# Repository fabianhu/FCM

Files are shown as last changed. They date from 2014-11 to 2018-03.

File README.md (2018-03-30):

FCM
===

FCM Flight Controller Firmware

Contents:

	Bootloader - the bootloader AVR32 project
	
	doc -  the main documentation folder -> read FCM Manual.pdf.
	
	hardware - here are the hardware sources. "hexa2wide" is our board. The actual physically produced board is under versions. This is the next release!
	
	software - the FCM copter control firmware main project

Size & weight:

	45 x 27 x 8 mm
	10 g

CPU:

	AVR32 UC3B0256
	32 bit
	48MHz

Sensors:

	Gyroscope (3 axis)
	Accelometer (3 axis)
	Magnetometer (3 axis)
	Barometer

Interfaces:

	4x PPM input or
	Receiver serial input for SPEKTRUM and HoTT or
	Receiver PPM sum signal input
	2x extra TTL USART (for Bluetooth, GPS, Telemetry etc.)
	6x PPM output for speed controllers (SimonK firmware recommended)
	optocoupler for 5 PPM outputs (placement variant)
	Pulse input for ultrasonic distance measurement
	USB for configuration and updates

Software features:

	FabOS32 RTOS
	Quaternion based attitude control
	Altitude hold
	Any copter configuration via mixing matrix
	RC compatibility
	HoTT SUMD receiver signal
	SPEKTRUM sattelite receiver signal
	4-channel "any RX" classic mode
	PPM sum signal
	USB Bootloader
	GPS integration with waypoint processing and return-to-home
	Throw to start
	
Telemetry

	HoTT telemetry with settings menue
	Bluetooth telemetry with settings menue, Attitude and graph display
	MAVlink prepared
	PID setting via extra RC analog channels

Software is "closed source" = all own code with minor extensions with LGPL
	Software is now open-sourced under GPL V3

Visit also the projects:
	FCM-android and
	FCM-Manager

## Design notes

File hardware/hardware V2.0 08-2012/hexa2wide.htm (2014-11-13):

Stückliste exportiert aus C:/Users/Fabi/Desktop/quadcopter_svn/versions/hardware V2.0 08-2012/hexa2wide.sch am 13.09.2012 19:53:36

Menge | Wert | Device | Bauteile
1 | | R-EU_R0603 | RL
7 | 2.2uF | C-EUC0603K | C4, C12, C13, C15, CA4, CP3, CR3
7 | 2k2 | R-EU_R0402 | R3, R6, R7, R8, R9, RS1, RS2
2 | 4µ7 | C-EUC0805 | CA2, CU1
3 | 4WIRE_CONN | 4WIRE_CONN | U$10, U$11, U$12
1 | 8MHz | CRYSTALCTS406 | Q1
1 | 10n 25V | C-EUC0402 | CR2
2 | 18pF | C-EUC0402 | CQ1, CQ2
2 | 39 | R-EU_R0402 | R1, R2
13 | 100n | C-EUC0402 | C1, C5, C6, C7, C14, CA1, CP1, CP2, CP4, CP5, CP6, CPR, CR1
1 | 220n | C-EUC0402 | CA3
8 | 330 | R-EU_R0402 | R11, R13, R15, R17, R19, RL1, RL2, RL3
1 | AT32UC3B0 | AT32UC3B0 | U$1
1 | BMP085 | BMP085 | U$9
1 | L3G4200DHAND | L3G4200DHAND | U$5
1 | LSM303HAND | LSM303HAND | U$7
1 | MCP1824ST-3302E/DB | MCP1824ST-3302E/DB | U1
1 | QS6J1=FDC6312P | QS6J1=FDC6312P | T1
1 | TLP283 | TLP283 | OK3
1 | TLP283-4 | TLP283-4 | OK1
5 | TPB1,27 | TPB1,27 | RST, TCK, TDI, TDO, TMS
6 | TPSQTP10SQ | TPSQTP10SQ | TP19, TP20, TP21, TP22, TP23, TP24
18 | TPSQTP16SQ | TPSQTP16SQ | TP1, TP2, TP3, TP4, TP5, TP6, TP7, TP8, TP9, TP10, TP11, TP12, TP13, TP14, TP15, TP16, TP17, TP18
1 | UBB_MICRO_HIROSE | UBB_MICRO_HIROSE | U$4
1 | blue | LEDCHIP-LED0603 | LED3
1 | green | LEDCHIP-LED0603 | LED2
1 | red | LEDCHIP-LED0603 | LED1

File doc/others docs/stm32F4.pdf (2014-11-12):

## stm32F4 Project

# 1. Description

## 1.1. Project

Project Name | stm32F4
Generated with: | STM32CubeMX 4.1.0
Date | 04/21/2014

## 1.2. MCU

MCU Serie | STM32F4
MCU Line | STM32F401
MCU name | STM32F401RETx
MCU Package | LQFP64
MCU Pin number | 64

# 2. Pinout Configuration

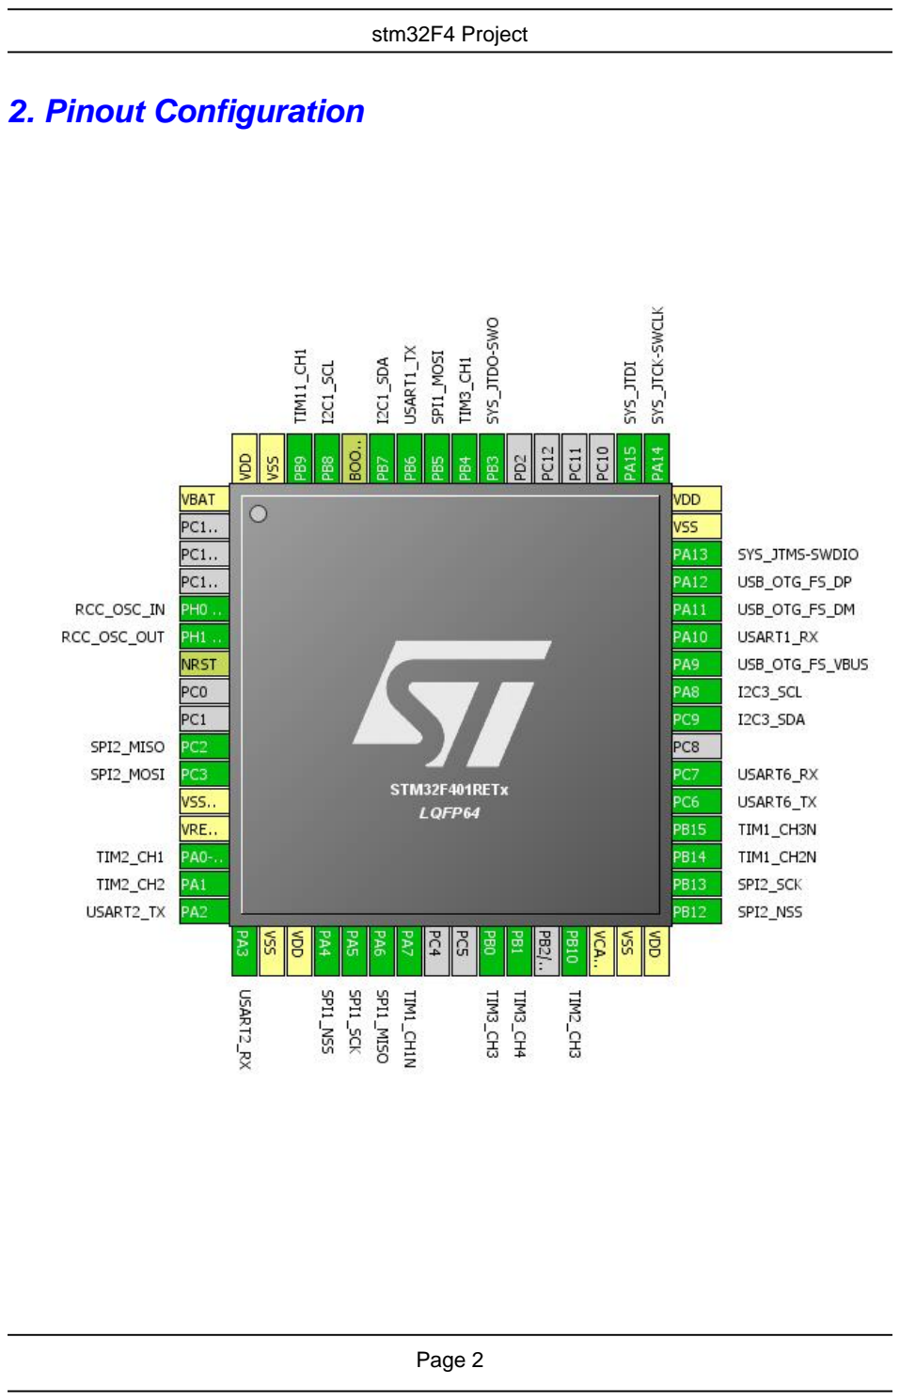
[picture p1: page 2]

# 3. IPs and Middlewares Configuration

IP | Mode | Fonction | Pin
CRC | Activated | N/A | N/A
I2C1 | I2C: I2C | I2C1_SCL | PB8
| | I2C1_SDA | PB7
I2C3 | I2C: I2C | I2C3_SCL | PA8
| | I2C3_SDA | PC9
IWDG | Activated | N/A | N/A
RCC | High Speed Clock (HSE): Crystal/Ceramic Resonator | RCC_OSC_IN | PH0 - OSC_IN
| | RCC_OSC_OUT | PH1 - OSC_OUT

SPI1

Mode:
Full-Duplex Master
| SPI1_MISO | PA6
| SPI1_MOSI | PB5
| SPI1_SCK | PA5
Hardware NSS Signal | SPI1_NSS | PA4

SPI2

Mode:
Full-Duplex Master
| SPI2_MISO | PC2
| SPI2_MOSI | PC3
| SPI2_SCK | PB13
Hardware NSS Signal | SPI2_NSS | PB12

SYS

Debug:
JTAG (4 pins)
SYS_JTCK-SWCLK | PA14
SYS_JTDI | PA15
SYS_JTDO-SWO | PB3
SYS_JTMS-SWDIO | PA13

TIM1

Trigger Source:
ITR0
N/A | N/A

Channel1:
Output Compare CH1N
TIM1_CH1N | PA7

Channel2:
Output Compare CH2N
TIM1_CH2N | PB14

Channel3:
Output Compare CH3N
TIM1_CH3N | PB15

TIM2

Trigger Source:
ITR0
N/A | N/A

Channel1:
PWM Generation CH1
TIM2_CH1 | PA0-WKUP

Channel2:
PWM Generation CH2
TIM2_CH2 | PA1

Channel3:
PWM Generation CH3
TIM2_CH3 | PB10

TIM3

Channel1:
PWM Generation CH1
TIM3_CH1 | PB4

Channel3:
PWM Generation CH3
TIM3_CH3 | PB0

Channel4:
TIM3_CH4 | PB1

IP | Mode | Fonction | Pin
| PWM Generation CH4
TIM11 | Activated | N/A | N/A
| Channel1: Output Compare CH1 | TIM11_CH1 | PB9
USART1 | Mode: Asynchronous | USART1_RX | PA10
| | USART1_TX | PB6
USART2 | Mode: Asynchronous | USART2_RX | PA3
| | USART2_TX | PA2
USART6 | Mode: Asynchronous | USART6_RX | PC7
| | USART6_TX | PC6
USB_OTG_FS | Mode: Device_Only | USB_OTG_FS_DM | PA11
| | USB_OTG_FS_DP | PA12
| Activate_VBUS | USB_OTG_FS_VBUS | PA9
WWDG | Activated | N/A | N/A
MiddleWare | Mode
USB_DEVICE | Class For FS IP: CDC_FS

# 4. Pins Configuration

Pins | Pos | Functions
PH0 - OSC_IN | 5 | RCC_OSC_IN
PH1 - OSC_OUT | 6 | RCC_OSC_OUT
PC2 | 10 | SPI2_MISO
PC3 | 11 | SPI2_MOSI
PA0-WKUP | 14 | TIM2_CH1
PA1 | 15 | TIM2_CH2
PA2 | 16 | USART2_TX
PA3 | 17 | USART2_RX
PA4 | 20 | SPI1_NSS
PA5 | 21 | SPI1_SCK
PA6 | 22 | SPI1_MISO
PA7 | 23 | TIM1_CH1N
PB0 | 26 | TIM3_CH3
PB1 | 27 | TIM3_CH4
PB10 | 29 | TIM2_CH3
PB12 | 33 | SPI2_NSS
PB13 | 34 | SPI2_SCK
PB14 | 35 | TIM1_CH2N
PB15 | 36 | TIM1_CH3N
PC6 | 37 | USART6_TX
PC7 | 38 | USART6_RX
PC9 | 40 | I2C3_SDA
PA8 | 41 | I2C3_SCL
PA9 | 42 | USB_OTG_FS_VBUS
PA10 | 43 | USART1_RX
PA11 | 44 | USB_OTG_FS_DM
PA12 | 45 | USB_OTG_FS_DP
PA13 | 46 | SYS_JTMS-SWDIO
PA14 | 49 | SYS_JTCK-SWCLK
PA15 | 50 | SYS_JTDI
PB3 | 55 | SYS_JTDO-SWO
PB4 | 56 | TIM3_CH1
PB5 | 57 | SPI1_MOSI
PB6 | 58 | USART1_TX
PB7 | 59 | I2C1_SDA
PB8 | 61 | I2C1_SCL
PB9 | 62 | TIM11_CH1

# 5. Power Plugin report

## 5.1. Microcontroller Selection

Serie | STM32F4
Line | STM32F401
MCU | STM32F401RETx
Datasheet | 025644_Rev1

## 5.2. Parameter Selection

Temperature | 25
Vdd | 1.8

## 5.3. Battery Selection

Battery | Li-SOCL2(DD36000)
Capacity | 36000.0 mAh
Self discharge | 0.08 %/month
Nominal voltage | 3.6 V
Max Cont Current | 450.0 mA
Max Pulse Current | 1000.0 mA

## 5.4. Sequence

Step | STEP1
Mode | RUN
Range | Scale2-Medium
Fetch type | FLASH/ART_ON NO_PREFETCH
Clock Config. | HSE PLL_ON
Clock Source Freq. | 4.0 MHz
CPU Freq. | 84.0 MHz

Periph. | CRC GPIOA GPIOB GPIOC GPIOH I2C1 I2C3 SPI1 SPI2 SYS TIM1 TIM2 TIM3 TIM11 USART1 USART2 USART6 USB_OTG_FS WWDG
Additional Cons. | 0 mA
Average Current | 17.54076 mA
Duration | 1 ms
DMIPS | 105.0

## 5.5. Results

Sequence time | 1.0 ms | Average current | 17.541 mA
Battery Life | 2 months , 25 days & 7 hours | Average DMIPS | 105.0 DMIPS

## 5.6. Chart

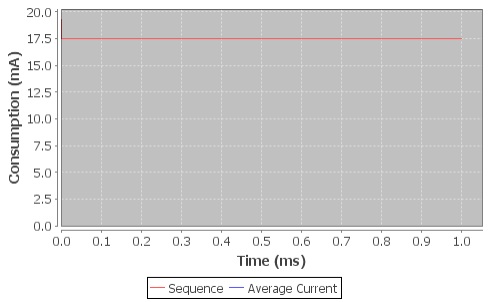
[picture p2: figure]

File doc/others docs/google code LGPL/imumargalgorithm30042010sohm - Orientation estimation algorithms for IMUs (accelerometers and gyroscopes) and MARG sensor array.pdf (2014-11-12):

Project Home | Downloads | Wiki | Issues | Source
My favorites ▼ | Sign in

# imumargalgorithm30042010sohm

Orientation estimation algorithms for IMUs (accelerometers and gyroscopes) and MARG sensor arrays (accelerometers, gyroscopes and magnetometers)

Summary People

Project Information

+8 Recommend this on Google

Project feeds

Code license
GNU Lesser GPL

Labels
IMU, MARG, AHRS, gyroscope, accelerometer, magnetometer, orientation

Members
sebmadgwick@googlemail.com

Links
External links
IMU demo video
MARG demo video
Camera control application video IMU tag v1.0 AHRS demo project

IMPORTANT

This code project is now maintained at:

http://www.x-io.co.uk/open-source-imu-and-ahrs-algorithms/

The project provides the source code for the algorithms developed and discussed in the report, "An efficient orientation filter for inertial and inertial/magnetic sensor arrays".

The available downloads (tab above) include: The internal report (pdf) with source code in appendix; the Visual Studio 2008 projects used to create the IMU and MARG demo videos; an image (pdf) detailing the physical sensor axis alignments of the Sparkfun 6DOF IMU Razor and HMC5843 breakout board; and the x-io Board firmware (hex and readme in zip) required by the MARG demo to interface to the HMC5843.

Report abstract:

"This report presents a novel orientation filter applicable to IMUs consisting of tri-axis gyroscopes and accelerometers, and MARG sensor arrays that also include tri-axis magnetometers. The MARG implementation incorporates magnetic distortion and gyroscope bias drift compensation. The filter uses a quaternion representation, allowing accelerometer and magnetometer data to be used in an analytically derived and optimised gradient-descent algorithm to compute the direction of the gyroscope measurement error as a quaternion derivative. The benefits of the filter include: (1) computationally inexpensive; requiring 109 (IMU) or 277 (MARG) scalar arithmetic operations each filter update, (2) effective at low sampling rates; e.g. 10 Hz, and (3) contains 1 (IMU) or 2 (MARG) adjustable parameters defined by observable system characteristics. Performance was evaluated empirically using a commercially available orientation sensor and reference measurements of orientation obtained using an optical measurement system. A simple calibration method is presented for the use of the optical measurement equipment in this application. Performance was also benchmarked against the propriety Kalman-based algorithm of orientation sensor. Results indicate the filter achieves levels of accuracy exceeding that of the Kalman-based algorithm; <0.6 degrees static RMS error, <0.8 degrees dynamic RMS error. The implications of the low computational load and ability to operate at low sampling rates open new opportunities for the use of IMU and MARG sensor arrays in real-time applications of limited power or processing resources or applications that demand extremely high sampling rates."

Demonstration videos:

http://www.youtube.com/watch?v=Egl75nv9E7s (IMU algorithm)

http://www.youtube.com/watch?v=fOSTOnQzZCI (MARG algorithm)

http://www.youtube.com/watch?v=7GVXqNLLH7Q (Example application: camera control/stabilisation)

Terms - Privacy - Project Hosting Help

Powered by Google Project Hosting

imumargalgorithm30042010sohm - Orientation estimation algorithms f... | http://code.google.com/p/imumargalgorithm30042010sohm/
1 von 1 | 14.02.2013 00:38

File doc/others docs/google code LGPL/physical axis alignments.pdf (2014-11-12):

IMU z-axis = LY530A z-axis | IMU x-axis = LPR530A y-axis | IMU y-axis = (-) LPR530A x-axis

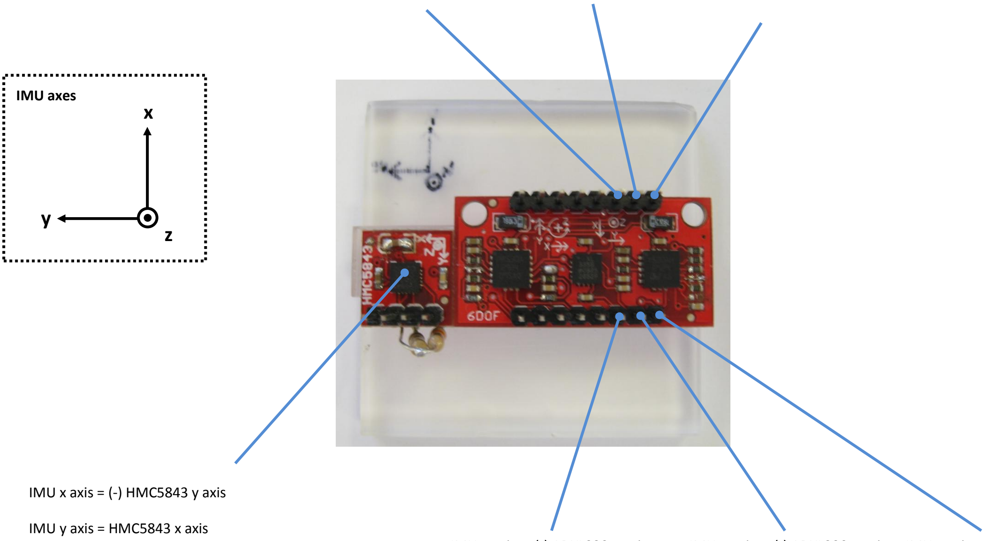
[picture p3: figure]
IMU x axis = (-) HMC5843 y axis; IMU y axis = HMC5843 x axis; IMU axes

IMU x-axis = (-) ADXL330 x-axis | IMU y-axis = (-) ADXL330 y-axis | IMU z-axis = ADXL330 z-axis
IMU z axis = HMC5843 z axis

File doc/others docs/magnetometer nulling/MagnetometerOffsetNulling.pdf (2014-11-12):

Magnetometer offset cancellation | - 1 - | April 11, 2010

Magnetometer Offset Cancellation: Theory and Implementation

William Premerlani, April 11, 2010

Problem: Magnetometers have non-zero offsets from a combination of effects, including local magnetic fields in the body frame, and offsets in the electronics. It is desired to have a simple way to determine the offsets, and subtract them out.
Solution: Enlist the aid of the direction cosine matrix to determine the offsets.
Theory:
It is assumed that the magnetometer’s gains are calibrated, it is just the offsets we are worried about. For example, the HMC5843 3-Axis magnetometer has a self-test feature that determines calibration, but it does not have any way to determine the offsets.
It is possible to determine the offsets in flight. As the aircraft (plane or heli) rotates, the direction cosine matrix is good indication of its changes in orientation. The offsets are constant in the body frame of reference. The earth’s magnetic field is constant in the earth frame of reference. The total measured magnetic field is the sum of the two fields. Using matrix algebra, it is possible to determine the offsets of the magnetometer.
The starting point is the direction cosine matrix, R, which relates magnetic fields in earth and body frame of reference:

the transpose of the direction cosine matrix the direction cosine matrix

magnetic field measurement in body frame magnetic field measurement in earth frame

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
b | R b
b | R b

equation 1

There are two components of the measurement, the earth’s magnetic field, and the magnetometer offsets:

magnetometer offset

earth's magnetic field
=

=

0

C
b

b
equation 2

In the body frame of reference, the measured magnetic field vector is related to the offsets and the earth’s magnetic field as follows:

C

T bB = b0 + R ⋅b | equation 3

By itself, equation 3 does not help us determine the offsets from a single measurement report from the magnetometer. However, we have a stream of measurements coming out of the magnetometer as the aircraft changes orientation. Similar to the technique used in wind estimation, although we cannot rely on the direction-cosine-matrix to give us absolute orientation, it is rather accurate in giving us changes in orientation. We can use

Magnetometer offset cancellation | - 2 - | April 11, 2010

those changes, and a stream of measurements, to continually update and null out the offsets.
Start with a pair of measurements, taken at time 1 and time 2. Suppose the orientation of the aircraft has changed. (If it does not change, then the offsets do not matter!) Then we have two instances of equation 3:

C

T
B | 0 | 2

C

T
B | 0 | 1
b | b | R b
b | b | R b
| = + | ⋅
= + | ⋅

2

1 | equation 4

Multiplying through by the direction cosine matrix from the left, we find:

2 | B | 2 | 0 | C
1 | B | 1 | 0 | C
R b | R b b
R b | | R b b
⋅ | = | ⋅ +
⋅ | = | ⋅ +

2

1 | equation 5

Subtracting the two equations just given, we find:
( | ) R2 bB | R1 bB | R2 | R1 | b0 ⋅ | − ⋅ | = | − | ⋅ 2 | 1 | equation 6

At this point, we might be tempted to invert the matrix on the right hand side of equation 6, but we would be falling into a trap, because its determinant is identically 0. So we cannot do that. Some thought will reveal the reason why the determinant is 0, and will give us an approach to nulling the offset anyway.
Consider the case in which the aircraft rotates around the Z axis. This will give us information only about the X and Y offsets, but tells us nothing about the Z axis offset. Similarly, equation 6 gives us information only about the offset in the plane that is perpendicular to the rotation from position 1 to position 2. Still, the information in that plane is useful, because it is all we need to null the offset in that plane, and we can wait until there is a change in orientation that gives us information in other planes to give us the complete picture. So, we can use equation 6 to obtain the component of the offset that is perpendicular to the rotation axis. Before stating the solution to equation 6, it is useful to first define the relative rotation between the two orientations and its transpose:

R 1 R1 R2

R R R

T T
2

1

T
21 2
= | ⋅
= | ⋅ | equation 7

Now, we can solve equation 6 for the component of the offset that is perpendicular to the axis of rotation from orientation 1 to 2. (The interested reader might want to give it a try.)
[ | ]
() 21

B2

T
B1 | B2 | 21 | B1 | 2

### 0 R

b | b | R b | R b b | −Trace
+ | − | ⋅ | + | ⋅ ⊥ = | 3
1 | equation 8

The function “Trace” operating on a matrix returns the sum of the diagonal elements. This is the first time I have ever used this operator. I am delighted.
Equation 8 is an exact solution to equation 6. But we do not need an exact solution. What we need is something that we can feed into an integrator that will gradually drive the offsets to zero. The numerator of equation 8 is a vector that we can use to drive the offset vector in the correct direction. It is convenient to multiply equation 8 by the denominator of the right hand side. After we do that, we will have a vector in the correct direction,

Magnetometer offset cancellation | - 3 - | April 11, 2010

multiplied by a gain that rises and falls with the amount of rotation that the aircraft is experiencing. This is just the thing that we want, more gain when it is rotating, less gain than when it is not. So, now we have a negative feedback recipe for driving the offsets to zero in flight.
We will maintain an up to date estimate of the magnetic offset vector of the magnetometer:
estimate of the magnetometer offset bˆ
0 = | equation 9

Each time we make a magnetometer measurement, we will subtract the offset before we report it:
bB | bmagnetometer | b0 = | − ˆ | equation 10

We will use the adjusted values in the direction cosine matrix drift correction. We will also use pairs of adjusted values and their associated direction cosine matrices to compute an update for the estimate of the offset vector:
( | ) [ | ] B2
T b0 | b0 | bB1 + bB2 − R21 ⋅bB1 + R2 ⋅b ∆ = + | 1 ˆ | ˆ
τ

t
equation 11

Delta t is the time step, tau is the desired time constant of the adjustment. The elegance of equation 11 is that we can execute it for every new magnetometer measurement, whether the aircraft is changing orientation or not. If it is not changing orientation, nothing will happen, because the right hand side of equation 11 will be zero. We will not be driving the offset to zero, but it does not matter, because we are not changing direction anyway. If the aircraft is rapidly changing orientation, then the right hand side of equation 11 will be large, and will quickly drive the offset to zero, exactly when we need to do that. Implementation
Implementation of equation 11 is straightforward. The only special case we have to be careful about is when the aircraft is sitting on the ground and not moving at all. In that situation, equation 11 should return identically zero, but because of roundoff, there can be a bias, which would gradually ramp up the offset estimates. The errors would dissipate quickly once the aircraft began moving, but it would be best to prevent them in the first place. That is easy enough to do by simply putting a small deadband in the integration of equation 11.
The following is the implementation of equation 11, as well as the yaw compensation of the direction cosine matrix, in a magnetometer demo written for the UAV DevBoard. Note that the yaw compensation takes only 6 lines, it is a lot easier to do in terms of direction cosines than it is in terms of tilt-compensating the magnetometer in terms of Euler angles.
The bulk of the code is for computing the magnetometer offsets:

Magnetometer offset cancellation | - 4 - | April 11, 2010

void mag_drift()
{
int mag_error ;
int vector_index ;
fractional rmatTransposeMagField[3] ; fractional offsetSum[3] ;
fractional deltaMagField[3] ;
if ( flags._.mag_drift_req )
{
setDSPLibInUse(true) ;
// Compensate the DCM algorithm for drift: magFieldEarth[0]=VectorDotProduct(3,&rmat[0],magFieldBody )<<1 ; magFieldEarth[1]=VectorDotProduct(3,&rmat[3],magFieldBody )<<1 ; magFieldEarth[2]=VectorDotProduct(3,&rmat[6],magFieldBody )<<1 ; mag_error=100*VectorDotProduct(2,magFieldEarth,declinationVector) ; VectorScale( 3 , errorYawplane , &rmat[6] , mag_error ) ;

// Compute the offsets in the magnetometer:
VectorAdd( 3 , offsetSum , magFieldBody , magFieldBodyPrevious ) ; for ( vector_index = 0 ; vector_index < 3 ; vector_index++ )
{
offsetSum[vector_index] >>= 1 ;
}
MatrixMultiply(1,3,3,
rmatTransposeMagField,magFieldEarthPrevious,rmat) ; VectorSubtract(3 ,offsetSum,offsetSum,rmatTransposeMagField ) ; MatrixMultiply(1,3,3,
rmatTransposeMagField,magFieldEarth,rmatPrevious) ; VectorSubtract(3,offsetSum,offsetSum,rmatTransposeMagField) ; for ( vector_index = 0 ; vector_index < 3 ; vector_index++ ) {
int adjustment ;
adjustment = offsetSum[vector_index] ;
if ( abs( adjustment ) < 3 )
{
offsetSum[vector_index] = 0 ; adjustment = 0 ;
}
offsetDelta[vector_index] = adjustment ; }
if ( flags._.first_mag_reading == 0 )
{
VectorAdd ( 3 , magOffset , magOffset , offsetSum ) ; }
else
{
flags._.first_mag_reading = 0 ;
}
VectorCopy ( 3 , magFieldEarthPrevious , magFieldEarth ) ; VectorCopy ( 3 , magFieldBodyPrevious , magFieldBody ) ; VectorCopy ( 9 , rmatPrevious , rmat ) ; setDSPLibInUse(false) ;
flags._.mag_drift_req = 0 ;
}
return ;

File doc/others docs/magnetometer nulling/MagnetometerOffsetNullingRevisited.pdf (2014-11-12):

Magnetometer offsets revisited | - 1 - | October 14, 2011

Magnetometer Offset Cancellation: Theory and Implementation, revisited
William Premerlani, October 14, 2011

This is a re-examination of a problem discussed by this author in a previous paper, with a new solution.

Problem: Magnetometers have non-zero offsets from a combination of effects, including local magnetic fields in the body frame, and offsets in the electronics. It is desired to have a simple way to determine the offsets, and subtract them out.

Solution: Use the apparent variation of the magnitude of the magnetic field to determine offsets.

Theory:
It is assumed that the magnetometer’s gains are calibrated, it is just the offsets we are worried about. For example, both the HMC5843 and the HMC5883L 3-Axis magnetometers have a self-test feature that determines calibration, but it does not have any way to determine the offsets.
It is possible to compensate for the offsets in flight.
In a previous paper the approach was based on using the rotation information in the direction cosine matrix to compute and remove magnetometer offsets. However, during recent work to compensate for magnetometer misalignment, I discovered that misalignment causes errors in the previously reported method for removing offsets. It is possible to compensate for misalignment, and there will soon be a separate report on that subject. By compensating for misalignment, it is possible to restore the accuracy of the offset removal. However, if you prefer not to compensate for misalignment, there is another method for removing offsets that works well in the face of misalignment.
An alternate approach is to focus on the magnitude of the magnetic measurements. Assuming both a magnetic offset vector and a misalignment rotation matrix, the magnetic measurement in the body frame can be expressed as follows:

rotation matrix representing misalignment

and the direction cosine matrix and its transpose magnetic field measured in body frame

actual magnetic field in the earth frame

=

=

=

=

= + ⋅ ⋅

A

R R

b

b

b | b | A R b

T

B

E

E

T
B 0

equation 1

Equation 1 can be rewritten as:

E

T bB − b0 = A⋅R ⋅b | equation 2

Magnetometer offsets revisited | - 2 - | October 14, 2011

The square of the magnitude of a vector is found by taking its dot product with itself, which can be expressed in matrix notation as multiplying the transpose of the vector by itself:
( | )( | )

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
b | b | A R b | A R b
=
− | = ⋅ | ⋅ | ⋅ ⋅ | ⋅ | equation 3

In other words, because both matrices in equation 3 are rotation matrices, their transpose is equal to their inverse, and they preserve vector magnitudes. Therefore, the magnitude of the difference between each magnetic measurement minus the magnetic offset must be a constant.
Expand the left side of equation 3. We find:

2

### 0 E

T
B

2
0

2
bB | + b | − 2⋅b ⋅b = b | equation 4

Now, take measurements in two different attitudes, put them into two instances of equation 4, subtract and rearrange. We find:
( | ) 0
| | T B

T
B

2
B

2
bB2 | − b 1 | = 2 | equation 5 ⋅ b 2 −b 1 ⋅b

Equation 5 does not tell us what the offset vector is equal to. But we do not need to know exactly what it is in order to gradually cancel it. What we can do is gradually refine our estimate of the offset. Equation 5 gives us enough information to compute the refinements.
Equation 5 defines a plane in 3 dimensions. We can tell from equation 5 on what side of the plane the offset vector must be. A reasonable refinement is in a direction perpendicular to the plane. In that case, we find a good guess at a step in the right direction is given by:
( | ) ( | )

estimate of the offset ˆ

ˆ | ˆ | 1
2 | 1
2 | 1

=

⋅ | − −
− = + | ⋅

0

B2 B
B B

B B
0 0

b

b | b
b | b
b | b b | b | gain
equation 6

The gain parameter is selected to strike a reasonable balance between numerical stability and speed of convergence. I used a value of 1 for gain in my implementation, but you might want to experiment with other values.
What equation 6 says to do is to divide the difference vector between two magnetic measurements by its magnitude (in other words, normalize the vector), multiply by the difference of the magnitudes of the two measurements, and multiply by the convergence gain. Then, add the refinement to the estimate of the offset. The offset estimate is then removed from each measurement.
The way that the method works is that each refinement is in the approximate correct direction. As the estimate improves, the difference in the second factor goes to zero, and the estimate must converge to the correct value. Each time the aircraft rotates a little bit, the magnetic measurement will change. If there is any change in the magnitude of the

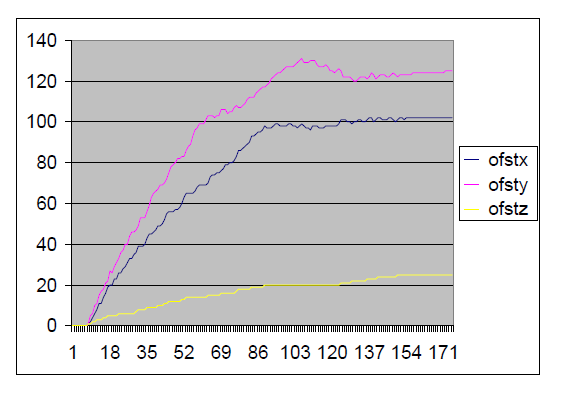
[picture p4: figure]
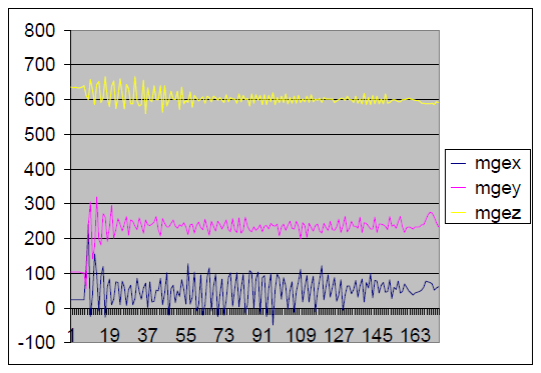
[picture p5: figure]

Magnetometer offsets revisited | - 3 - | October 14, 2011

measurement, that is an indication of an offset. Application of equation 6 gradually completely removes the offset.
Some of you might be worried by the division by the magnitude of the difference of the measurements. In practice, that is not a problem, provided you do not do the division if the denominator is zero. In that case, the second factor in equation 6 will be zero anyway, so the computed refinement will come out to be zero.
I have performed extensive tests of offset removal using equation 6, and found convergence to be rapid and accurate. A typical plot of the computed offsets during a spin test at 78 RPM is shown in Figure 1. The computed values are converging to the values that I measured manually.

Figure 1 Computed offsets using equation 6 The measured magnetic field vectors with offsets removed and rotated back into the earth frame of reference while the IMU and magnetometer were spinning at 78 RPM are shown in Figure 2.

Magnetometer offsets revisited | - 4 - | October 14, 2011
Implementation
Implementation is trivial. Here is the section of the MatrixPilot code that updates the offset vector estimate:

magFieldBodyMagnitude = vector3_mag( udb_magFieldBody[0], udb_magFieldBody[1], udb_magFieldBody[2] ) ; VectorSubtract( 3, vectorBuffer , udb_magFieldBody , magFieldBodyPrevious ) ;
vector3_normalize( vectorBuffer , vectorBuffer ) ; VectorScale( 3 , offsetEstimate , vectorBuffer , magFieldBodyMagnitude - magFieldBodyMagnitudePrevious ) ;

udb_magOffset[0] = udb_magOffset[0]
+ ( ( offsetEstimate[0] + 2 ) >> 2 ) ;
udb_magOffset[1] = udb_magOffset[1]
+ ( ( offsetEstimate[1] + 2 ) >> 2 ) ; udb_magOffset[2] = udb_magOffset[2]
+ ( ( offsetEstimate[2] + 2 ) >> 2 ) ;

The routines that are called do the following:
vector3_mag computes the magnitude of a vector.
VectorSubtract subtracts two vectors.
Vector3_normalize normalizes a vector to have magnitude equal to 1. VectorScale multiplies a vector by a scalar.

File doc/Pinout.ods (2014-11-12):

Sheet: Sheet1
 | unten | mitte | oben
8 | Signal 6 | plus | minus | Out 6 | 6 | + | -
7 | Signal 5 | plus | minus | Out 5 | 5 | + | -
6 | Signal 4 | plus | minus | Out 4 | 4 | + | -
5 | Signal 3 | plus | minus | Out 3 | 3 | + | -
4 | Signal 2 | plus | minus | Out 2 | 2 | + | -
3 | Signal 1 | plus in | minus | Out 1 | 1 | + | -
2 | RC2 | RC3 | RC4 | RC | 2 | 3 | 4
1 | RC1/ser RX | plus RC | minus | RC | 1 | + | -

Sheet: Sheet2
6 | + | - | ESC 6 opto | FCM 2.1 | huslik.net
5 | + | - | ESC 5 opto |  |  | USB
4 | + | - | ESC 4 opto
3 | + | - | ESC 3 opto
2 | + | - | ESC 2 opto
1 | + | - | ESC 1 / pwr |  |  | 3.3V
4 | 3 | 2 | RC |  |  | TX
1 | + | - | RC / serial | 3.3 V |  | RX
 |  |  |  |  |  | - | 3.3 V | please change hardware options here!
 |  |  |  |  |  |  | opto
6 | + | - | ESC 6 opto | FCM 2.1 | huslik.net
5 | + | - | ESC 5 opto |  |  | USB
4 | + | - | ESC 4 opto
3 | + | - | ESC 3 opto
2 | + | - | ESC 2 opto
1 | + | - | ESC 1 / pwr |  |  | 3.3V
4 | 3 | 2 | RC |  |  | TX
1 | + | - | RC / serial | 3.3 V |  | RX
 |  |  |  |  |  | -
6 | + | - | ESC 6 opto | FCM 2.1 | huslik.net
5 | + | - | ESC 5 opto |  |  | USB
4 | + | - | ESC 4 opto
3 | + | - | ESC 3 opto
2 | + | - | ESC 2 opto
1 | + | - | ESC 1 / pwr |  |  | 3.3V
4 | 3 | 2 | RC |  |  | TX
1 | + | - | RC / serial | 3.3 V |  | RX
 |  |  |  |  |  | -
6 | + | - | ESC 6 opto | FCM 2.1 | huslik.net
5 | + | - | ESC 5 opto |  |  | USB
4 | + | - | ESC 4 opto
3 | + | - | ESC 3 opto
2 | + | - | ESC 2 opto
1 | + | - | ESC 1 / pwr |  |  | 3.3V
4 | 3 | 2 | RC |  |  | TX
1 | + | - | RC / serial | 3.3 V |  | RX
 |  |  |  |  |  | -
6 | + | - | ESC 6 opto | FCM 2.1 | huslik.net
5 | + | - | ESC 5 opto |  |  | USB
4 | + | - | ESC 4 opto
3 | + | - | ESC 3 opto
2 | + | - | ESC 2 opto
1 | + | - | ESC 1 / pwr |  |  | 3.3V
4 | 3 | 2 | RC |  |  | TX
1 | + | - | RC / serial | 3.3 V |  | RX
 |  |  |  |  |  | -

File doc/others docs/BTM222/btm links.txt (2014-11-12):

http://robotrack.org/include.php?path=article&contentid=279
http://www.mikrokopter.de/ucwiki/BTM-222
http://robotrack.org/BTM222/BTM-indexD09.htm

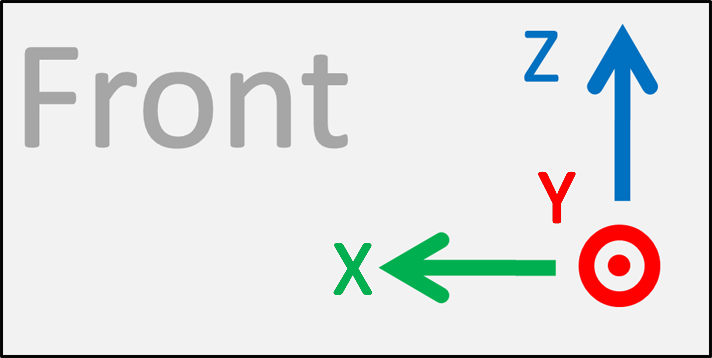
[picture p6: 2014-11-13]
binary releases/FCM_Manager 2.0.6/Form_3Dcuboid/Left.png

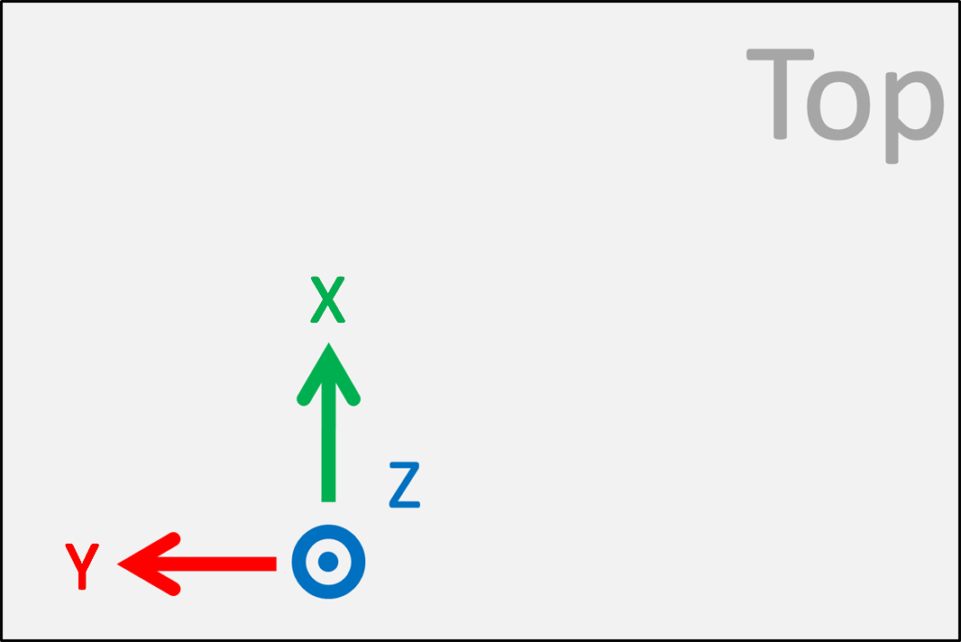
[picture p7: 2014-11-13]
binary releases/FCM_Manager 2.0.6/Form_3Dcuboid/Top.png

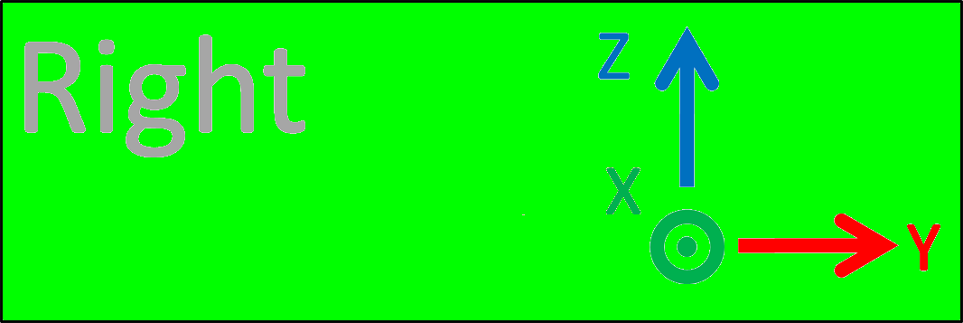
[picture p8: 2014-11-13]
binary releases/FCM_Manager 2.0.6/Form_3Dcuboid/Back.png

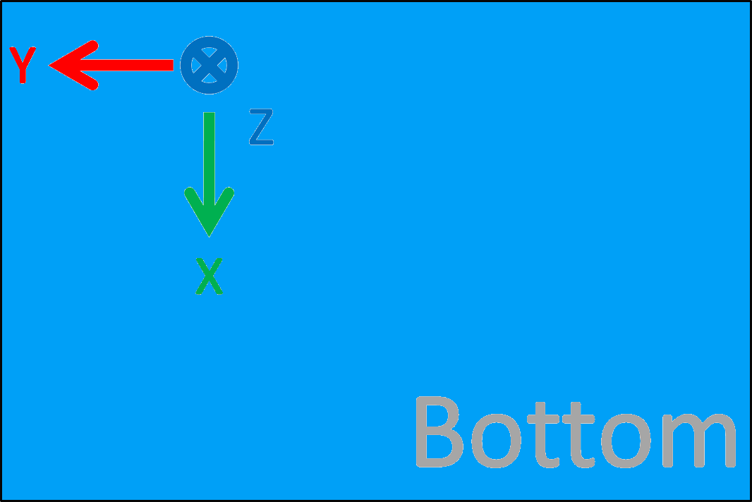
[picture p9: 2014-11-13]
binary releases/FCM_Manager 2.0.6/Form_3Dcuboid/Bottom.png

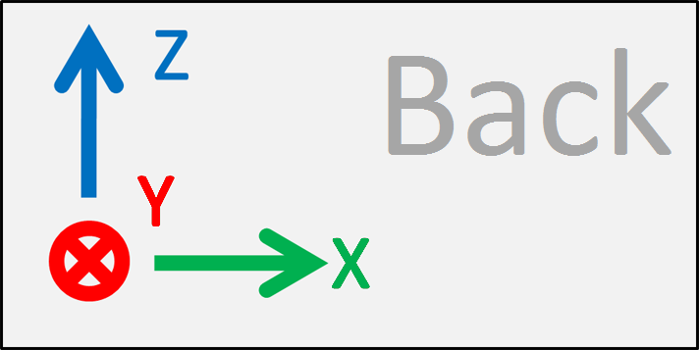
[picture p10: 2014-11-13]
binary releases/FCM_Manager 2.0.6/Form_3Dcuboid/Right.png

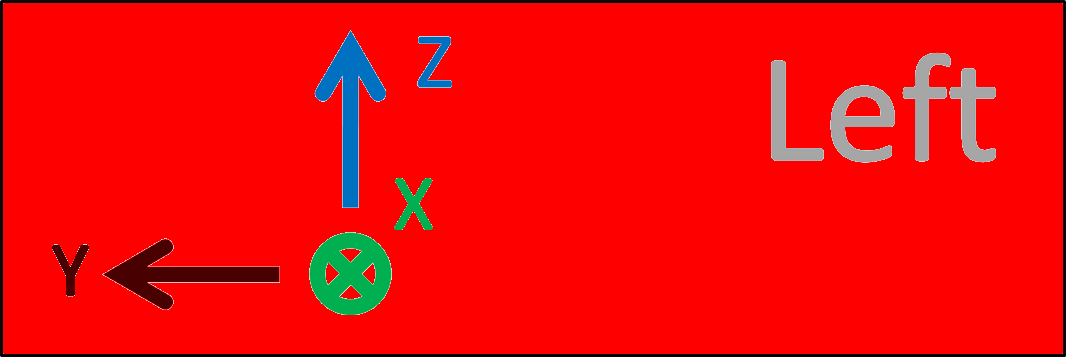
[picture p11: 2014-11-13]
binary releases/FCM_Manager 2.0.6/Form_3Dcuboid/Front.png

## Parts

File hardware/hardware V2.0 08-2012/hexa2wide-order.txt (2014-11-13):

Order list for C:/Users/Fabi/Desktop/quadcopter_svn/versions/hardware V2.0 08-2012/hexa2wide.sch
Exported from EAGLE with DesignLink

Anzahl	Value	Package	Ordercode	Hersteller	Herstellercode	Verfügbarkeit	Preis (ab)	Beschreibung
13	100n	C0402	1758896	MULTICOMP	MCCA000050	793694	0.0030	MULTICOMP - MCCA000050 - MLCC 0402, X7R, 16V, 100NF
7	2.2uF	C0603K	1735526	MURATA	GRM188R61C225KE15D	23760	0.05	MURATA - GRM188R61C225KE15D - KONDENSATOR, 0603, 2.2UF, 16V
2	4µ7	C0805	1845746	MURATA	GRM219R61C475KE15D	5992	0.046	MURATA - GRM219R61C475KE15D - KONDENSATOR, 0805, 4.7UF, 16V
1	220n	C0402	1572610	KEMET	C0402C224K9PACTU	29327	0.01	KEMET - C0402C224K9PACTU - KONDENSATOR, 220NF 6.3V X5R 0402
2	18pF	C0402	1828908	MURATA	GRM1885C1H180JA01D	9700	0.0090	MURATA - GRM1885C1H180JA01D - CAPACITOR, 0603, C0G, 50V, 18PF
1	10n 25V	C0402	1758924	MULTICOMP	MCCA000076	185872	0.0020	MULTICOMP - MCCA000076 - MLCC 0402, X7R, 25V, 10NF
1	red	CHIP-LED0603	1652080	AVAGO TECHNOLOGIES	ASMT-RR45-AQ902	77029	0.077	AVAGO TECHNOLOGIES - ASMT-RR45-AQ902 - LED,SMD,0603,ROT
1	green	CHIP-LED0603	1652078	AVAGO TECHNOLOGIES	ASMT-RF45-AN002	24328	0.077	AVAGO TECHNOLOGIES - ASMT-RF45-AN002 - LED,SMD,0603,GELB-GRUEN
1	blue	CHIP-LED0603	1685096	ROHM	SMLE12BC7TT86Q	4874	0.238	ROHM - SMLE12BC7TT86Q - LED,0603,LO-CUR. BLAU
1	TLP283-4	MINI-FLAT-16	1634758	AVAGO TECHNOLOGIES	ACPL-247-500E	20353	0.929	AVAGO TECHNOLOGIES - ACPL-247-500E - OPTOKOPPLER,QUAD,SMD,DC I/P
1	TLP283	MINI-FLAT-4	1602614	AVAGO TECHNOLOGIES	ACPL-217-500E	43268	0.179	AVAGO TECHNOLOGIES - ACPL-217-500E - OPTOKOPPLER,TRANSISTOR O/P
1	8MHz	CTS406	1611803	ABRACON	ABMM2-8.000MHZ-E2-T	17046	0.531	ABRACON - ABMM2-8.000MHZ-E2-T - QUARZ,8M, 18PF CL, 6X3.6MM SMT
2	39	R0402	1738831	VISHAY DRALORIC	CRCW040239R0FKEAHP	10692	0.0080	VISHAY DRALORIC - CRCW040239R0FKEAHP - WIDERSTAND, 0402, 1%, 39R0
7	2k2	R0402	9330399	MULTICOMP	MC 0.063W 0603 1% 10K	1357776	0.0090	MULTICOMP - MC 0.063W 0603 1% 10K - WIDERSTAND, 0603 10K
8	330	R0402	1469803	VISHAY DRALORIC	CRCW0603330RFKEA	51158	0.0040	VISHAY DRALORIC - CRCW0603330RFKEA - WIDERSTAND, 0603, 330R , 1%
1		R0603	1635693	WURTH ELEKTRONIK	74279266	21466	0.082	WURTH ELEKTRONIK - 74279266 - FERRIT, SMD 1000OHM, 0603
5	TPB1,27	B1,27	unknown					
1	QS6J1=FDC6312P	SUPERSOT-6	1700713	FAIRCHILD SEMICONDUCTOR	FDC6312P	636	0.255	FAIRCHILD SEMICONDUCTOR - FDC6312P - MOSFET P KANAL DUAL 2.3A 20V SSOT6
18	TPSQTP16SQ	TP16SQ	unknown					
6	TPSQTP10SQ	TP10SQ	unknown					
1	AT32UC3B0	JEDEC_MS-026	1715453	ATMEL	AT32UC3B0256-A2UT	634	6.9	ATMEL - AT32UC3B0256-A2UT - MCU32BIT,AVR32,256K FLASH, 64TQFP
1	UBB_MICRO_HIROSE	USB_MICRO	1645325	HRS (HIROSE)	ZX62-B-5PA(11)	6426	0.541	HRS (HIROSE) - ZX62-B-5PA(11) - BUCHSE,MICRO USB,TYP B
1	L3G4200DHAND	LGA16_HAND	unknown					
1	LSM303HAND	LGA14_HAND	2068595	STMICROELECTRONICS	LSM303DLHC	-6	3.79	STMICROELECTRONICS - LSM303DLHC - SENSOR,3 KANAL,ACCEL,MAG,MOD,14LGA
1	BMP085	BMP085	unknown					
3	4WIRE_CONN	4WIRE_PIN	unknown					
1	MCP1824ST-3302E/DB	SOT230P700X180-4N	1578379	MICROCHIP	MCP1824ST-3302E/DB	2078	0.443	MICROCHIP - MCP1824ST-3302E/DB - LDO,3.3V,300MA, SOT-223-3

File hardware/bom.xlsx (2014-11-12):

Lief | Buy | Need | Lager | Qty |  | Value | Device | Parts | BEST | MF | MPN | OC_FARNELL | OC_NEWARK | PACKAGE | SUPPLIER | TP_SIGNAL_NAME
china | 5 | 7 | 2 | 1 | unknown, 5, | BMP085 | BMP085 | U$9 |  |  |  | unknown
csd | 63 | 63 |  | 9 | 2140861RL, 63, CRCW040210K5FKED | 2k2 | R-EU_R0402 | R3, R4, R5, R6, R7, R8, R9, RS1, RS2 |  | VISHAY DRALORIC | CRCW040210K5FKED | 2140861RL
csd | 10 | 14 | 4 | 2 | 1845746, 10, GRM219R61C475KE15D | 4µ7 | C-EUC0805 | CA2, CU1 |  | MURATA | GRM219R61C475KE15D | 1845746
csd | 14 | 14 |  | 2 | 1572614RL, 14, C0402C180J5GACTU | 18pF | C-EUC0402 | CQ1, CQ2 |  | KEMET | C0402C180J5GACTU | 1572614RL
csd | 14 | 14 |  | 2 | 1738831, 14, CRCW040239R0FKEAHP | 39 | R-EU_R0402 | R1, R2 |  | VISHAY DRALORIC | CRCW040239R0FKEAHP | 1738831
csd | 7 | 7 |  | 1 | 2059179, 7, ERJ2RKF8062X | 80 | R-EU_R0402 | RL3 |  | PANASONIC | ERJ2RKF8062X | 2059179
csd | 91 | 91 |  | 13 | 1758896, 91, MCCA000050 | 100n | C-EUC0402 | C1, C5, C6, C7, C14, CA1, CP1, CP2, CP4, CP5, CP6, CPR, CR1 |  | MULTICOMP | MCCA000050 | 1758896
csd | 14 | 14 |  | 2 | 2140752, 14, CRCW0402604RFKED | 260 | R-EU_R0402 | RL1, RL2 |  | VISHAY DRALORIC | CRCW0402604RFKED | 2140752
csd | 35 | 35 |  | 5 | 2072931, 35, MCMR04X331 JTL | 330 | R-EU_R0402 | R11, R13, R15, R17, R19 |  | MULTICOMP | MCMR04X331 JTL | 2072931
csd | 7 | 7 |  | 1 | 1715453, 7, AT32UC3B0256-A2UT | AT32UC3B0 | AT32UC3B0 | U$1 |  | ATMEL | AT32UC3B0256-A2UT | 1715453
farnell | 5 | 7 | 2 | 1 | 1635693, 5, 74279266 |  | R-EU_R0603 | RL |  | WURTH ELEKTRONIK | 74279266 | 1635693
farnell | 2 | 7 | 5 | 1 | 1611803, 2, ABMM2-8.000MHZ-E2-T | 8MHz | CRYSTALCTS406 | Q1 |  | ABRACON | ABMM2-8.000MHZ-E2-T | 1611803 | unknown
farnell | 5 | 7 | 2 | 1 | 1578379, 5, MCP1824ST-3302E/DB | MCP1824ST-3302E/DB | MCP1824ST-3302E/DB | U1 |  | MICROCHIP | MCP1824ST-3302E/DB | 1578379 | 05N1293 | SOT-223-3 | Microchip
farnell | 7 | 7 |  | 1 | 1700713, 7, FDC6312P | QS6J1=FDC6312P | QS6J1=FDC6312P | T1 | Farnell 1525470 od 1700713 | FAIRCHILD SEMICONDUCTOR | FDC6312P | 1700713
farnell | 5 | 7 | 2 | 1 | 1634758, 5, ACPL-247-500E | TLP283-4 | TLP283-4 | OK1 |  | AVAGO TECHNOLOGIES | ACPL-247-500E | 1634758 | unknown
farnell | 3 | 7 | 4 | 1 | 1645325, 3, ZX62-B-5PA(11) | UBB_MICRO_HIROSE | UBB_MICRO_HIROSE | U$4 |  | HRS (HIROSE) | ZX62-B-5PA(11) | 1645325
farnell | 7 | 7 |  | 1 | 1685096, 7, SMLE12BC7TT86Q | blue | LEDCHIP-LED0603 | LED3 |  | ROHM | SMLE12BC7TT86Q | 1685096
farnell | 5 | 7 | 2 | 1 | 1652080, 5, ASMT-RR45-AQ902 | red | LEDCHIP-LED0603 | LED1 |  | AVAGO TECHNOLOGIES | ASMT-RR45-AQ902 | 1652080
mouser | 7 | 7 | 0 | 1 | 2295818, 7, L3GD20 | L3G4200DHAND | L3G4200DHAND | U$5 |  | STMICROELECTRONICS | L3GD20 | 2295818
mouser | 5 | 7 | 2 | 1 | 2068595, 5, LSM303DLHC | LSM303HAND | LSM303HAND | U$7 |  | STMICROELECTRONICS | LSM303DLHC | 2068595
x | -7 | 7 | 14 | 1 | 1602614, -7, ACPL-217-500E | TLP283 | TLP283 | OK3 |  | AVAGO TECHNOLOGIES | ACPL-217-500E | 1602614 | unknown
x | 0 | 7 | 7 | 1 | 1652078, 0, ASMT-RF45-AN002 | green | LEDCHIP-LED0603 | LED2 |  | AVAGO TECHNOLOGIES | ASMT-RF45-AN002 | 1652078
x | -1 | 49 | 50 | 7 | 1735526, -1, GRM188R61C225KE15D | 2.2uF | C-EUC0603K | C4, C12, C13, C15, CA4, CP3, CR3 |  | MURATA | GRM188R61C225KE15D | 1735526
x | -83 | 7 | 90 | 1 | 1758924, -83, MCCA000076 | 10n 25V | C-EUC0402 | CR2 |  | MULTICOMP | MCCA000076 | 1758924
x | 0 | 7 | 7 | 1 | 1572610, 0, C0402C224K9PACTU | 220n | C-EUC0402 | CA3 |  | KEMET | C0402C224K9PACTU | 1572610

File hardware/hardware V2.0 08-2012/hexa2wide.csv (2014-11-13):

Qty | Value | Device | Parts | BEST | MF | MPN | OC_FARNELL | OC_NEWARK | PACKAGE | SUPPLIER | TP_SIGNAL_NAME
1 |  | R-EU_R0603 | RL |  |  |  | unknown
7 | 2.2uF | C-EUC0603K | C4, C12, C13, C15, CA4, CP3, CR3 |  | MURATA | GRM188R61C225KE15D | 1735526
7 | 2k2 | R-EU_R0402 | R3, R6, R7, R8, R9, RS1, RS2 |  | MULTICOMP | MC 0.063W 0603 1% 10K | 9330399
2 | 4µ7 | C-EUC0805 | CA2, CU1 |  | MURATA | GRM219R61C475KE15D | 1845746
3 | 4WIRE_CONN | 4WIRE_CONN | U$10, U$11, U$12 |  |  |  | unknown
1 | 8MHz | CRYSTALCTS406 | Q1 |  | ABRACON | ABMM2-8.000MHZ-E2-T | 1611803 | unknown
1 | 10n 25V | C-EUC0402 | CR2 |  | MULTICOMP | MCCA000076 | 1758924
2 | 18pF | C-EUC0402 | CQ1, CQ2 |  | MURATA | GRM1885C1H180JA01D | 1828908
2 | 39 | R-EU_R0402 | R1, R2 |  | YAGEO (PHYCOMP) | RC0603FR-0739RL | 9238310
13 | 100n | C-EUC0402 | C1, C5, C6, C7, C14, CA1, CP1, CP2, CP4, CP5, CP6, CPR, CR1 |  | KEMET | C0402C104K4RAC AUTO | 2070374
1 | 220n | C-EUC0402 | CA3 |  | KEMET | C0402C224K9PACTU | 1572610
8 | 330 | R-EU_R0402 | R11, R13, R15, R17, R19, RL1, RL2, RL3 |  | VISHAY DRALORIC | CRCW0603330RFKEA | 1469803
1 | AT32UC3B0 | AT32UC3B0 | U$1 |  | ATMEL | AT32UC3B0256-A2UT | 1715453
1 | BMP085 | BMP085 | U$9 |  |  |  | unknown
1 | L3G4200DHAND | L3G4200DHAND | U$5 |  |  |  | unknown
1 | LSM303HAND | LSM303HAND | U$7 |  | STMICROELECTRONICS | LSM303DLHC | 2068595
1 | MCP1824ST-3302E/DB | MCP1824ST-3302E/DB | U1 |  | MICROCHIP | MCP1824ST-3302E/DB | 1578379 | 05N1293 | SOT-223-3 | Microchip
1 | QS6J1=FDC6312P | QS6J1=FDC6312P | T1 | Farnell 1525470 od 1700713 | FAIRCHILD SEMICONDUCTOR | FDC6312P | 1700713RL
1 | TLP283 | TLP283 | OK3 |  | AVAGO TECHNOLOGIES | ACPL-217-500E | 1602614 | unknown
1 | TLP283-4 | TLP283-4 | OK1 |  | AVAGO TECHNOLOGIES | ACPL-247-500E | 1634758 | unknown
5 | TPB1,27 | TPB1,27 | RST, TCK, TDI, TDO, TMS |  |  |  | unknown
6 | TPSQTP10SQ | TPSQTP10SQ | TP19, TP20, TP21, TP22, TP23, TP24 |  |  |  | unknown
18 | TPSQTP16SQ | TPSQTP16SQ | TP1, TP2, TP3, TP4, TP5, TP6, TP7, TP8, TP9, TP10, TP11, TP12, TP13, TP14, TP15, TP16, TP17, TP18 |  |  |  | unknown
1 | UBB_MICRO_HIROSE | UBB_MICRO_HIROSE | U$4 |  | HRS (HIROSE) | ZX62-B-5PA(11) | 1645325
3 | green | LEDCHIP-LED0603 | LED1, LED2, LED3 |  | KINGBRIGHT | KPG-1608ZGC | 1686061

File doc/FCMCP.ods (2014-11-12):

max frame length down 100 ; up 255
each frame starts with '---' and ends with '~~~'
all data are big endian (matching AVR32)
 | Format | Description
Commands
FCM | - | who is there, answer with FCM[version] | ---FCM~~~
STD[delay] | with optional delay for re-send: do not send for n cycles (*10ms) | Start streaming data | ---STD[delay]~~~
STQ[delay] | with optional delay for re-send: do not send for n cycles (*10ms) | Start streaming quaternion data | ---STQ[delay]~~~
STG[delay] | with optional delay for re-send: do not send for n cycles (*10ms) | Start streaming gps data | ---STG[delay]~~~
STS | - | Stop streaming data | ---STS~~~
MNU[command] | command 1 byte for keys tbd | Request menu update. answer with MNU#txt | ---MNU[command]~~~
BOOT | - | Jump into Bootloader | ---BOOT~~~
PARL | - | Get Parameter list (Answer PARL) | ---PARL~~~
PARV[ID][value] | 8 bit ID, 16 bit signed value | Set Parameter Value; answered with PAR[] | ---PARV[ID][value]~~~
Commands BOOTLOADER only
FCM | - | answer with FCM[version] Major 100+ for BL | ---FCM~~~
FER[adr][len] | 4 byte address, 4 byte len | Erase Flash | ---FER[adr][len]~~~
FWR[adr][len] | 4 byte address, 4 byte len | Positive answer is FWROK | ---FWR[adr][len]~~~
FRD[adr][len] | 4 byte address, 4 byte len | Data to be read follows as answer without header | ---FRD[adr][len]~~~
SER | - | Get serial number, Answered with 15 bytes SN | ---SER~~~
REB | - | Reboot | ---REB~~~
Responses
FCM[version] | version in binary 4 bytes (Bootloader response) | Major, Minor, Build (2 Bytes) | ---FCM[version]~~~
FCM[version][menusize] | version in binary 4 bytes + Menue size in 2 bytes | Major, Minor, Build (2 Bytes) | ---FCM[version][menusize]~~~
D[data] | see struct below (big endian!) |  | ---D[data]~~~
TXT[txt] | txt in chars; line break every 21 chars by PC; 8 lines fixed ! |  | ---TXT[txt]~~~
Q[data] | see struct below (big endian!) |  | ---Q[data]~~~
G
FERSD | - | Flash erase finished | ---FERSD~~~
FWROK | - | Flash write ready for data | ---FWROK~~~
FDONE | - | Flas write with announced length finished. | ---FDONE~~~
PAR[data] | n * {ID,Parent ID, Value 16bit, limit s, zero terminated text} | Parameter list items | ---PAR[data]~~~
'D' data format:
3x int32 | Gyro filtered
3x int32 | Accel filtered
3x int32 | Magnet filtered
3x int32 | Governor output
4x int32 | RC command
1x int32 | Height in mm
2x int16_t | Temperature in 10th °C
82 | Bytes
115200 | baud (max 921,5kbps)
140,487804878 | msg / s
'Q' quaternion format:
4x float | Measured attitude
4x float | Desired attitude
4x float | attitude error
3x int32 | Governor output
1x int32 | Height in mm
2x int16_t | Temperature in 10th °C
78 | Bytes
147,6923076923 | msg / s
'G' GPS data format
1x int32 | Longitude in 10.000.000th degrees
1x int32 | Latitude in 10.000.000th degrees
1x int32 | height (GPS)
1x float | x (lon) speed [m/s]
1x float | y (lat) speed [m/s]
1x float | z (up) speed [m/s]
1x float | x (lon) distance to target [m]
1x float | y (lat) distance to target [m]
1x float | z (up) distance to target [m]
1x uint8 | num of sattelites

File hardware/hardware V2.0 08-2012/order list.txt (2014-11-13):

Je eins:

Fabi Quadcopter
Fabi Flugzeug
Jörg
Uli
Christian

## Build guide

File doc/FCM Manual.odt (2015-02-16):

FCM developers manual

(c) 2013-2015 Fabian Huslik

This work is licensed under the
Creative Commons Attribution-ShareAlike 4.0 International License.
To view a copy of this license, visit
http://creativecommons.org/licenses/by-sa/4.0/.

# Introduction

This is a rudimentary attempt to write down, what is going on in FCM.

The most accurate documentation is the source code itself and the schematic with layout.

The only thing, you really can rely on in this document, are the axis definitions in

"5 Definitions & Copter Layout".

# License

If not otherwise stated in the source files, most of the code is copyrighted as follows:

Copyright (c) 2008-2015 by Fabian Huslik

Some other but not less important parts:

MadgwickAHRS / MahonyAHRS: Copyright (c) 2011 by SOH Madgwick

menu: Copyright (c) 2010-2014 by Jörg Schmidt & Fabian Huslik

hottv4: Copyright (c) 08/2012 by Adam Majerczyk

BMP085 driver: Copyright (C) 2009 Bosch Sensortec GmbH

printf: Copyright (c) 2004,2012 Kustaa Nyholm / SpareTimeLabs

ASF Framework: Copyright (c) 2009-2014 Atmel Corporation. All rights reserved.

Mavlink: Copyright Lorenz Meier and contributors

FCM Android: Copyright (c) 2014 Joachim Weishaupt

License details for each file are specified inside the source files.

For the documentation and hardware design the following applies:

This work is licensed under the Creative Commons Attribution-ShareAlike 4.0 International License. To view a copy of this license, visit http://creativecommons.org/licenses/by-sa/4.0/.

# Bootloader

To activate bootloader, plug in the FCM via USB and THEN power it up. Hardware version 2.1 is not USB powered, so external 5V is needed.

During bootup, the bootloader looks for USB voltage (5V). If USB is found, the bootloader mode is activated and the main application will not start.

- Blue on and green blinking with 5 Hz: waiting for USB
- Blue blinking with 3 Hz: USB serial port connected.
- Red lit: flash write access.
- 3-colour cycling: Application has started. See FAQ

The USB-waiting-mode will be repeated, if no application is loaded.

To load a hex file, go to FCM_Manager and click on "connect". If the bootloader responds , the "load HEX file" button gets activated.

select "load HEX file".

Do not forget to compile the hex file for YOUR configuration beforehand.

Adjust settings in config.h

Parameters will be preserved only, if nothing in the parameter config has changed.

Save your parameters using the FCM_Manager BEFORE flashing.

The FCM_Manager lets you know, when it's finishes with success.

It does only take a few seconds to load the hex file.

When finished, disconnect USB and cycle power supply.

## USB Drivers

The USB drivers are located in the "Bootloader/Bootloader" directory. Just point windows to this directory, if the board is connected for the first time.

## Installing USB Bootloader on Board

Do this in order:

1. Erase the controller
2. Flash the bootloader hex file (in bootloader directory, there is only one)
3. set fuse bootloader flash size to 16kByte.
4. Do not set the BOD fuse, this will be activated in SW!

# Building FCM hardware

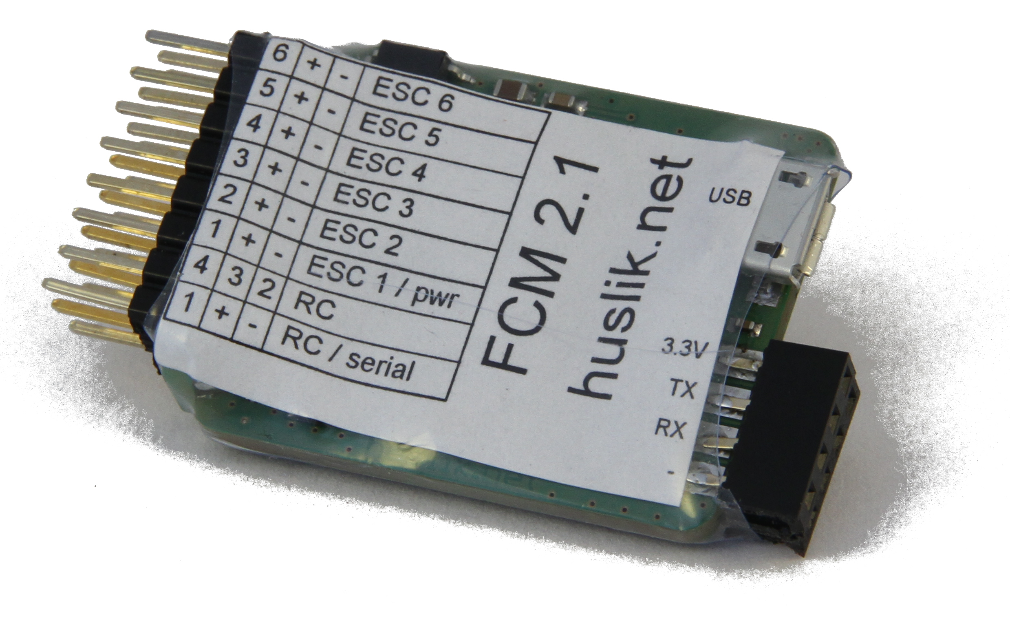
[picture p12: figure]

The schematics of the latest hardware can be found at:

versions\hardware V2.0 08-2012\hexa2wide.pdf

The "trunk" already contains hardware adaptations for the next version.

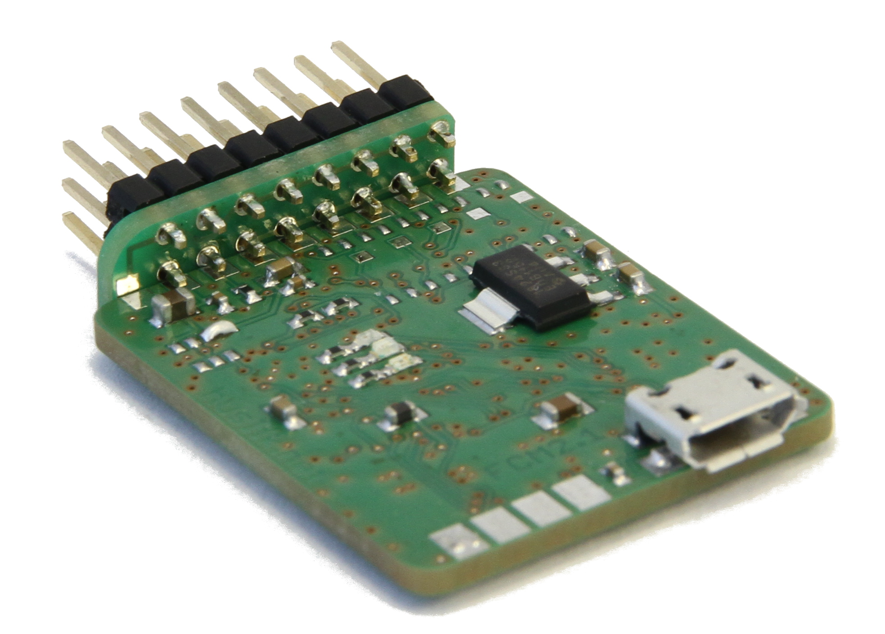
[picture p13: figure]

FCM consists of two PCBs. The small PCB carries the connectors and is fixed to the big one at the front. Solder the big PCB between the two lower connector rows. Solder the two extra pads at the left (botton and top)

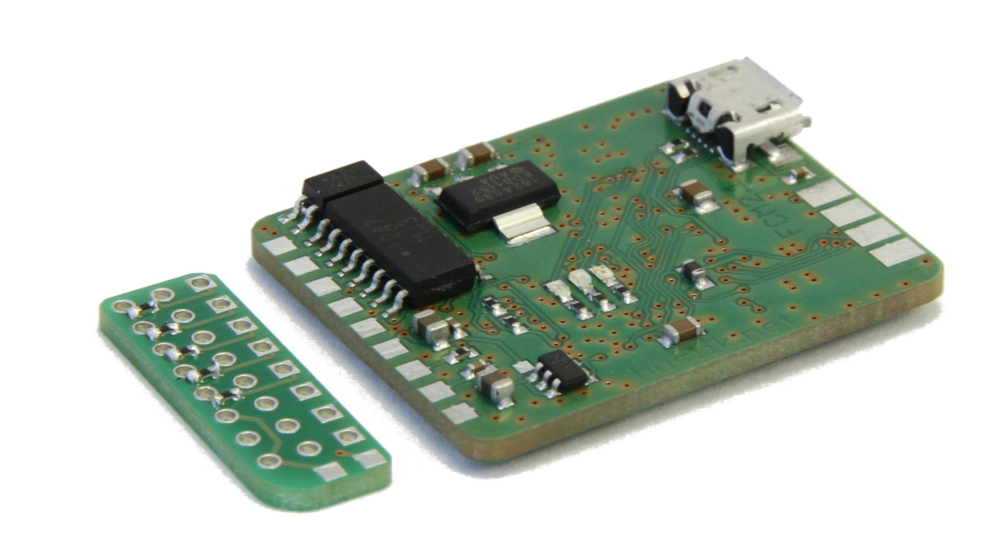
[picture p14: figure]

## Placement variant Receiver supply

For SPEKTRUM sattelite operation a P-channel MOSFET "T1" is placed, so that the 3.3V supply become switchable by FCM.

To enable 5V supply for the receiver, connect TP24 to the adjacent MOSFET pad. Usually a solder blob will do the job.

## Placement variant with optocouplers

For opto version use the small PCB with resistor pads, Place 5x 2k2 resistors before soldering the pin headers. Use only little solder for the pin headers before fixing it to the main PCB.

## Placement variant without optocouplers

If the optocouplers are not required, do not place them, place instead 5x 2k2 resistors from the TP19..23 test points to the LED Anode pad. The "other" small PCB without resistor pads has to be used, where all supplies are connected.

## Final assembly

Use a 1 mm piece of ABS to cover the lower part of the PCB. The components are selected for equal height.

Fix the printed paper cover to the small pcb with a little (hot) glue

Shrinkwrap the whole thing.

Fix it to your copter with double-sided foam adhesive as explained in 7 Installation on Copter.

# Definitions & Copter Layout

For a printout of axis definition, see later in this manual.

## Motor layout - top view:

(1) (2) ^

X |

(4) (3) dir of flight

(1) (2) ^

(6) X (3) |

(5) (4) dir of flight

## Motor turning directions:

(+) (-) + = right

X - = left

(-) (+)

(+) (-) + = right

(-) X (+) - = left

(+) (-)

## Axes positive directions for Vehicle:

Axis Acceleration Rotation

X: left to right around x backward

Y: back to front around Y right

Z: bottom to top around Z CCW (looking from above)

Rotation directions follow the right hand rule from each axis direction!

## Axes for Board:

Connectors for RX and ESCs face into flight direction.

Flat side with CPU faces down.

## Servo input scaling

throttle = 1000 = idle - 9000 full

roll: -4000 = right +4000 = left

elev : +4000 nose down -4000 nose up

yaw: -4000 = right +4000 = left

# External electrical connection

GND is up!

Connect power supply to the "ESC1" connector. Connecting to the Receiver input may fry your board (3.3V-supply in SPEKTRUM version)

From left (seen in flight direction)

( 1 + - ) RC / serial : Receiver with power supply and Serial / PPM or "classic" channel 1

( 4 3 2 ) "classic" channels 2,3,4 or special function

( 1 + - ) The first ESC with BEC, which also supplies the 5V power for the FCM

( 2 + - ) ESC with BEC (supplies only opto)

( 3 + - ) ESC with BEC (supplies only opto)

( 4 + - ) ESC with BEC (supplies only opto)

( 5 + - ) ESC with BEC (supplies only opto)

( 6 + - ) ESC with BEC (supplies only opto)

At the no-opto variant there is obviously no galvanic separation.

The Comm ports are left of the USB connector.

USART0 is up (Telemetry)

USART2 is bottom side (GPS)

Pins LTR: GND, rx, tx, +3.3V

Telemetry (no matter which type) goes to the upper connector.

GPS goes to the LOWER connector.

Absolute max total load at all 3.3V outputs is 200 mA at 5V supply.

# Installation on Copter

## Mechanical alignent

FCM must be installed flat with the RX and motor connectors facing straight forward.

Up to now, there is no rotation offset possible.

Align the FCM perpendicular to vehicle axises. (naah the multiple of axis..)

## Magnetometer considerations

- Absolutely NO current loops on motor / battery / ESC wires
- Twist all wires and ensure equal length
- The bigger the distance of the FCM to the high current wires, the better.
- The influence is reduced with the squared distance.
- Even batteries can emit a significant magnetic field at high currents.

Try in "direct mode" with the fixed copter and watch the magnetometer values using telemtery. They should not move by more than a few percent of the max-min value during motor running. (To be honest, if the fluctuations are less than one third of the signal span, flight could be possible).

## Vibration considerations

Vibration has a big effect on sensor performance. Especially the accelerometer will see all vibration.

Signs of a vibration issue could be poor levelling performance.

Therefore some tips to prevent vibration related issues:

- Balance your props as good as possible
- Balance your props in all dimensions (some props have a significant imbalance perpendicualar to the blades – the short way, which you wouldnt expect)
- Center your props (some hubs require 0.1mm additional sheet or some tape to center perfectly)
- Mount the FCM on the 2mm white foam (if no problems exist)
- Mount the FCM on 3mm black foam rubber (if there is residual vibration)
- If there is still unresolvable vibration, reduce the area of foam (cut out two stripes or leave a hole at center)
- Do not mount FCM too softly, as it will not directly follow the airframe movement, which leads to oscillation
- A loosened FCM will lead to a uncontrollable vehicle.
- Make sure, that there are no resonances on the airframe. (GPS-Antenna on long pole etc...)

# Source code management

We use github at the location

https://github.com/fabianhu/FCM/

If you are allowed to commit to the repo, please feel free to do so.

PLEASE write in commit message, what you did.
Most important stuff in first line, add a '+' at the end of the first line, if you provide a multi-line commit message, which is highly appreciated.

Or use the github facilities to open an issue or a pull request.

If you need an idea, what to do, look at the todo.txt in the "doc" directory .

# Parameter Description

Default values for small (800g) quad in "()".

The following text is auto-generated out of the Treebuilder.exe !!! The single source for this is the *.jmdef file.

GYRO PID Gyroscope based Governor settings

| <back>

| Max Integr Max Integrator windup (4000)

| Gov at Max Governor intensity at max power [%] (20)

| Q Gain Quaternion turn rate (4000)

| *Swash as Poti Use Potis as PID settings for Swash (xy)

| Swash P (60)

| Swash I (37)

| Swash D (37)

| *Yaw as Poti Use Potis as PID settings for Yaw (z)

| Yaw P (58)

| Yaw I (21)

| Yaw D (16)

NAV Navigation Governor Parameters

| <back>

| NAV Limits Navigation Governor Parameters

| | <back>

| | Max Angle The max lean angle in degrees (30)

| | Max Accel The max acceleration out of nav in 1/10 m/s^2 (2)

| | Max Acc int The max acceleration integrator windup out of nav in 1/10 m/s^2 (2)

| | Radius NAV The radius in meters, at which the cruise speed starts to decelerate (20)

| | Radius h The radius in meters, at which the height change speed starts to decelerate (20)

| NAV Filters Navigation Governor Parameters

| | <back>

| | Acc Flt glob global acceleration filter value (1000) 1000 is unfiltered

| | alpha pos complementary filter for position (???) 0 is prio for GPS

| | alpha spd complementary filter for position (???) 1000 is accel prio

| NAV Compensation Navigation Compensation

| | <back>

| | Comp On Activate the compensation algorithm

| | Min Speed Minimum speed, at which the vectoring calculation starts (1)

| | Min Time Minimum time en route, after which the vectoring calculation starts (5)

| | Filter 100 is unfiltered

| | Min Distance Minimum distance from target to activate the compensation

| *NAV as Poti Use Potis as PID settings

| NAV P (25)

| NAV I (0)

| NAV D (30)

| *H as Poti Use potis as PID settings for height governor

| H P (300)

| H I (50)

| H D (1000)

Settings General settings

| <back>

| Max Power Max throttle (6500)

| Idle Power Min throttle, use above 1500 for idle running props

| Agility fact How aggressive the copter reacts to RC (1-2)

| wait GPS Fix 1 = Flight is only released if GPS is fixed

| No BT222 cfg 1 = skip BTM222 initialisation sequence at start

| Direct Mode 1 = NO Flight control, throttle directly without unlock to all ESC! Use this to calibrate all ESCs at once. Negative numbers = single motor control, others off

| SPEKTRUM DSMX 1= try bind in DSMX mode

| *Bnd SPEKTRUM Do bind Spectrum Sattelite at RC-Port

| *Start Bootloader Go into bootloader mode

Calibration Sensor calibration

| <back>

| Filters Sensor calibration

| | <back>

| | Gyro Filter Gyroscope filter: 1= unfiltered (1)

| | Accel Filter Accelerometer filter: 1= unfiltered (4)

| | Magneto Flt Magnetometer filter: 1= unfiltered (4)

| | Baro Filter Barometer filter: 1000= unfiltered (990)

| | GPS Filter GPS filter: 1000= unfiltered (990)

| *Calibrate R+A Calibrate Gyro and Accelometer ? put on flat surface!

| Gyro X Gyro calibration value

| Gyro Y Gyro calibration value

| Gyro Z Gyro calibration value

| Acc X Accelometer calibration value

| Acc Y Accelometer calibration value

| Acc Z Accelometer calibration value

| MagCal flght Magnetometer calibration during engines on allowed ? (0)

| Mag X Magnetometer calibration value (via online calibration)

| Mag Y Magnetometer calibration value (via online calibration)

| Mag Z Magnetometer calibration value (via online calibration)

RC Channels RC channel assignment. Go to diag mode to see results.

| <back>

| Sw PosHold Which channel is used for Pos hold (ch #)

| SwP PosHold At which pos is the function active (0=lo 1=mid 2=hi) Pos Hold wins over RTH!

| Sw H Gov Which channel is used for height governor on (ch #)

| SwP H Gov At which pos is the function active (0=lo 1=mid 2=hi)

| Sw RTH Which channel is used for Return To Home (ch #)

| SwP RTH At which pos is the function active (0=lo 1=mid 2=hi)

| Sw Aux Which channel is used for Auxiliary function (ch #)

| SwP Aux At which pos is the function active (0=lo 1=mid 2=hi)

| Poti P Which channel is used for P potmeter

| Poti I Which channel is used for I potmeter

| Poti D Which channel is used for D potmeter

*Save to Flash Saves all settings values to flash

*Diag mode Display diag page (press enter to leave)

Test This is magic stuff... will disappear later.

| <back>

| Madgwick

| alpha Madg x 0.01 --> 100 = 1.0 (10)

| prop Mah x 0.01 --> 100 = 1.0 (50)

| integr Mah x 0.01 --> 100 = 1.0 (10)

| test P

| test I

| test D

| wind

| | wind_freq

| | wind_ampl

| | <back>

| mag_mis

| | mag_mis_freq

| | mag_mis_ampl

| | <back>

| gyro

| | gyro_freq

| | gyro_ampl

| | <back>

| accel

| | accel_freq

| | accel_ampl

| | <back>

| magneto

| | magneto_freq

| | magneto_ampl

| | <back>

# Firmware internals

The "secret" keywords are:

"fixme" for things, that should be fixed soon or require some more analysis.

"todo" for things, that may be unfinished or prepared new features or just have much room for improvements.

All variables starting with "debug" should have no functional meaning and should be removed in the future.

## Folder structure

The FCM flight-Software is in "software".

All sources are in "src".

In the long run, all .h and .c files should move into modular sub-folders.

in "src" the following important folders exist:

menu : here is all menue related

modules: here the "beautiful" code is put, that means, it has somehow clear interfaces.

## Menue editing

For editing the menue, use ONLY the "Treebuilder.exe" from the software folder.

The menue content is stored in "quadcopter.jmdef".

If changing a node, do not forget to press "change"

If finished with editing, click on generate and safe the "quadcopter.jmdef" file over the old one.

After generating, click into the left output window, this will put the content into the windows clipboard. Paste it into the menu_variant.h file lower part. Some editors (as the Atmel Studio) insert line breaks. You may have to remove these after inserting. You will see on build...

The menue description for each node is also edited in TreeBuilder. It comes out again as comments with the generated code and also as text to be inserted into this document in 9 Parameter Description.

## Adaptations for your copter

In the file config.h are some important switches. These are explained there.

The miximg matrix is defined in /src/modules/servo_out.c. Look at the existing variants.

## Building a hex file

Use Atmel Studio 6.2.1153 with

Atmel AVR (32 bit) GNU Toolchain – 3.4.2.1057 Version: AVR32_Toolchain_Version:3.4.2.435 GCC_VERSION:4.4.7

Atmel Software Framework - 3.19.0.1334

You need to have TortoiseSVN installed for the pre-build script to work.

Do not change any linker or compiler settings, it is working beautifully as adjusted.

The first instruction goes to 0x80004000, The bootloader will jump there for start.

You may switch off the '-pedantic' option, if you get too many warnings. Ignore all warnings, which are telling "... is a GCC extension".

There are some adaptions inside the framework files regarding the trampoline and exception table (scall) – so be careful with updating the framework not to kill the stuff.

## Communication protocol

Please see FCMCP.ods.
The parameter part of MAVlink is implemented and working.

# Math – some hints

Excellent source for all math in 3D: http://www.euclideanspace.com/maths/index.htm

another "primer" for quaternions: http://www.cprogramming.com/tutorial/3d/quaternions.html

## The master plan

(copy of New Governor Math.odg)

PID lat 9DOF IMU Attitude
actual Set bank
global delta Euler
rotation * PID PID PID bank y Mix + Motors scalar quaternion initial PID lon dv y dv x bank x Vset y Vset x Set-
Speed Distance V act Set
global * Set heading GPS RC

An efficient orientation filter for inertial and

inertial/magnetic sensor arrays

Sebastian O.H. Madgwick

April 30, 2010

The most promising source: (LGPL – but not only because of this)

madgwick_algorithm_c.zip with

madgwick_internal_report.pdf

## Quaternion math in code

Look at /modules/quaternion.c

## How to get the "difference" of two Quaternions

Just "multiply" them.

Which means, take the first rotation and rotate it further by the second.

## How to filter Gyro, Acc and Mag into one "My actual attitude" quaternion:

Madgwick or Mahony it. There is some sensor fusion involved.

## Some other IMU source – just for reference:

GPLV3:

https://code.google.com/p/gentlenav/downloads/list

# BTM222 Hints

Referring to the BTM222 datasheet for the pinout, solder the following:

This is a TOP view !!!

Put the wires to the bottom! (the 2 – 17 jumper can stay at top)

Pin 2 + Pin17 = 3.3V supply

Pin 29 = GND (all other required GNDS are already connected to the tin shield)

Pin 26 = connect to FCM TX

Pin 27= connect to FCM RX

Pin 37 = connect a wire of more or less exactly 30.7mm measured from the BTM222 edge (cut after soldering)

To clean superfluous com ports:

Create a batch file and execute as admin with:

set devmgr_show_nonpresent_devices=1

set devmgr_show_details=1

start DEVMGMT.MSC

Then select "show unused devices" and remove the stuff.

# Thanks

Many thanks go to my great beta testers:

Uli

Joachim

Jörg

Armin

Christian

# MbAQ Might be Asked Questions or FAQ

## What are the blink codes:

- red on, blue&green blinking alternating: No RC signal
- running light: not ready (throttle zero, no GPS lock or FCM not level)
- red on and blue&green blinking together: fatal error state: count number of blinks and search for "emstop(n)", where n is the number of blinks.
- Green blinking: ready to be armed with yaw right and throttle 0
- blue steady on: flight; may be disarmed with yaw left and throttle 0

## LSM303DLHC magnetometer not working

If the LSM303DLHC delivers irregular values (too low, only one axis working or so...):

check the external capacitor CA2 or CA3. One of these IS failed.
Thats easier than changing the chip, as I did first, which of course didn't solve the problem.

## Whats this nice diagram on the last page?

That's the truth. Believe it.

We use a ENU orientation for all 3d stuff. Right handed!

The navigation is done in a x-y = E-N order, where the rotation is right positive.

All this might be changed to the NED standard later. But anyway, there is no standard.

Z

up

N 0°

LAT Y

O 90°

LON X

S 180°

W 270°

Y forward

X right

2D Navigation

3D Orientation

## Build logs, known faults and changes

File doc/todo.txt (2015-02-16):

Die Anleitung:

- noch neu machen
+ noch testen
* fertig und läuft
# Konzept nötig

____________________________________________________________________________________________________
Hardware 2.2:
+ Pitch 2,75 für die Stecker statt 2,54mm !!
- Eine SMD-3x-LED, statt 3 einzelne
- Pads für + und - zum Jtag-anlöten - braucht's eher nicht, da an den seriellen Ports gut erreichbar.
- Belegung der seriellen Ports so wählen, daß eine Verpolung nicht toastet.
- Dickes C (nur fürs gute Gefühl)
+ USB-Supply über Diode

Hardware 3.0:
- Umstieg auf ARM STM32F4 !
Schnittstellen hinzu: 
	- SPI für Daughter-board
	- TWI für externen Magneto
MS5611 oder LPS25HB oder LPS22HB (Nachfolger) als baro
LSM9DS1 oder LSM9DS0 als IMU

____________________________________________________________________________________________________
SW machen

http://www.camelsoftware.com/firetail/blog/uavs/quaternion-ahrs-and-centrifugal-force/

- FabOS komplett 32-bitten
- MAVlink Nachrichten für OSD machen
- GPS return to home
- Magnetometer per Parameter abschaltbar
* Lageregler (Quaternion-basiert)
+ Höhenregler
+ Externe Interrupts (RC-in) wieder gängig machen
- Windows-Teil "gescheit" machen, Mutlithreading, Bootloader: Binary Rücklesen und vergleichen.
- Brown out im BL aktivieren (Flash canceln?)
- Missweisungs-Korrektur hinzu (Fehlwinkel zw. gewünschter und aktueller Bewegungsrichtung)

____________________________________________________________________________________________________
FCM-Manager

- safe to flash command 

____________________________________________________________________________________________________
irgendwann: 

- Ultraschall-Eingang: TC -> Höhenmessung
* HoTT GPS emulation an den Start bringen
# Parameterbeschreibung über Tool

____________________________________________________________________________________________________
erledigt:

* Beim Flashen geht die Kalibrierung flöten oder der ACCEL stürzt ab. (Watchdog?)
* parameter refresh
* disconnect button
* remember com port
* Reset nach Download bzw. für Einstieg in BL
* Watchdog anstarten
* Bootloader testen
* Serial Ports alle über ein interface
* HoTT senden in extra Task; Menu - generierung über zentralen Menü-Task machen.
* Startup-Prozedur / Status / Ausrichten Istwert und Übernahme Sollwert
* BOM 0402-Teile als 0402 bestellen, nicht 0603.
* Kalibrierung Magneto
* Luftdruck in Höhe umrechnen (in Bodennähe)
* Treiber für ACC schreiben
* Treiber für Magneto
* Sensor Fusion zw. ACC und Gyro
* BT Treiber
* Treiber für Luftdruck
* FCM2.1 austesten (ACC)
* Control Tasks und Erfassungs-Tasks machen, synchronisieren und die Daten �bertragen
* Timer f�r Servo-Zeitmessung aktivieren und verwenden
* Wiederholte Konfiguration des CMA3000(Acc) wieder raus, schauen, warum's dann nicht geht.
* re-init der Chips bei Ausfall, oder verd�chtigen 0-0-0-Werten
* ctl_main() Kommentare ausprogrammieren (ctl.c)
* Gyro und Acc filtern, da� wir bei ca. 20Hz GF landen
* Regelungszeugs an den Start bringen
* PWM-Interrupt f�r die Datensammlung von den beiden Chips aktivieren& schneller samplen
  (kommt dann mit ca. 2kHz vom Gyro und max 400Hz vom Acc.) 
* ST Gyro Treiber schreiben (L3G4200D / L3GD20)
* kP, Ki und Kd "irgendwie" verstellbar machen Infrarot ???? ;-)
* 1ms-Tick ISR f�r FabOS anmachen *** fertig, aber ungetestet. Fab
* FabOS portieren
* Verhindern, dass nach dem Anstecken ohne Sender alles anl�uft. (Timeout / plaus RC in)
- ADC anwerfen f. Messung Akkuspannung 
* Warning "input is not relaxable" bek�mpfen.

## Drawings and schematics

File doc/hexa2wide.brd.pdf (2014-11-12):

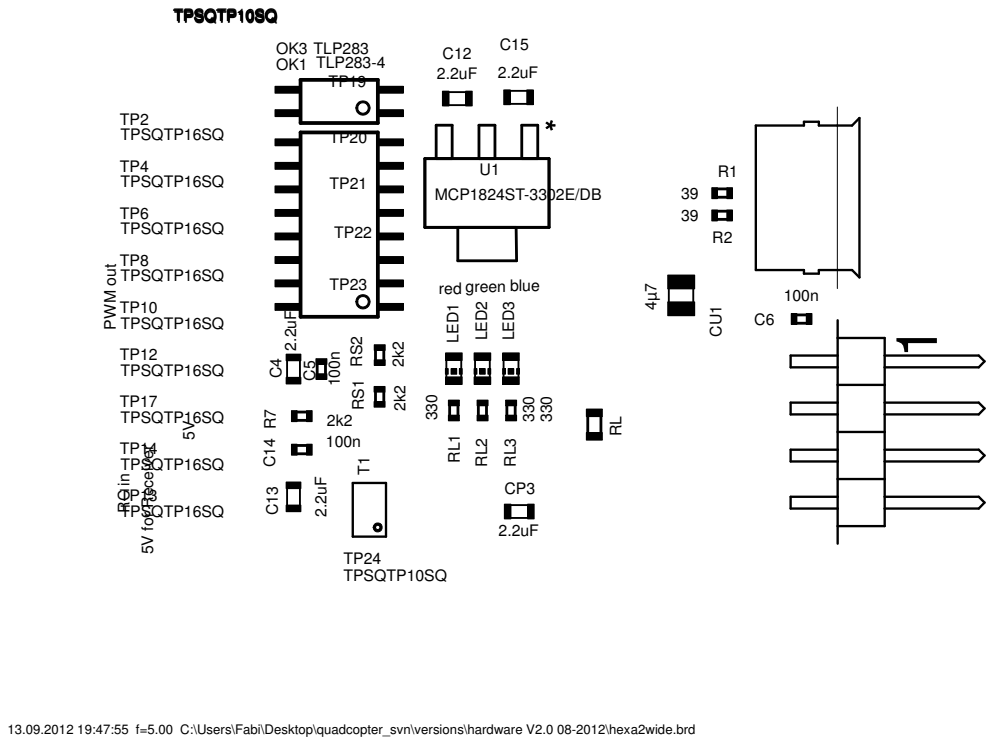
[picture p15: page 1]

13.09.2012 19:47:55 f=5.00 C:\Users\Fabi\Desktop\quadcopter_svn\versions\hardware V2.0 08-2012\hexa2wide.brd

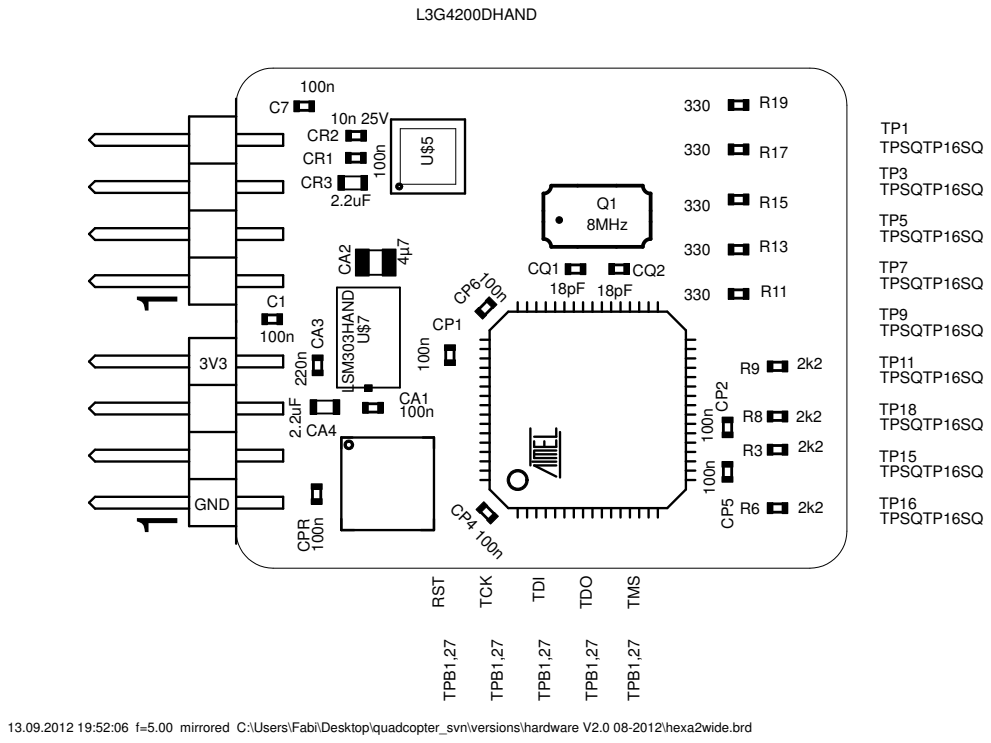
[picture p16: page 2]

13.09.2012 19:52:06 f=5.00 mirrored C:\Users\Fabi\Desktop\quadcopter_svn\versions\hardware V2.0 08-2012\hexa2wide.brd

Stückliste exportiert aus C:/Users/Fabi/Desktop/quadcopter_svn/versions/hardware V2.0 08-2012/hexa2wide.sch am 13.09.2012 19:53:36

Menge Wert | Device | Bauteile
1 | | R-EU_R0603 | RL
7 | 2.2uF | C-EUC0603K | C4, C12, C13, C15, CA4, CP3, CR3
7 | 2k2 | R-EU_R0402 | R3, R6, R7, R8, R9, RS1, RS2
2 | 4µ7 | C-EUC0805 | CA2, CU1
3 | 4WIRE_CONN | 4WIRE_CONN | U$10, U$11, U$12
1 | 8MHz | CRYSTALCTS406 | Q1
1 | 10n 25V | C-EUC0402 | CR2
2 | 18pF | C-EUC0402 | CQ1, CQ2
2 | 39 | R-EU_R0402 | R1, R2
13 | 100n | C-EUC0402 | C1, C5, C6, C7, C14, CA1, CP1, CP2, CP4, CP5, CP6, CPR, CR1
1 | 220n | C-EUC0402 | CA3
8 | 330 | R-EU_R0402 | R11, R13, R15, R17, R19, RL1, RL2, RL3
1 | AT32UC3B0 | AT32UC3B0 | U$1
1 | BMP085 | BMP085 | U$9
1 | L3G4200DHAND | L3G4200DHAND | U$5
1 | LSM303HAND | LSM303HAND | U$7

### 1 MCP1824ST-3302E/DB MCP1824ST-3302E/DB U1

1 | QS6J1=FDC6312P | QS6J1=FDC6312P | T1
1 | TLP283 | TLP283 | OK3
1 | TLP283-4 | TLP283-4 | OK1
5 | TPB1,27 | TPB1,27 | RST, TCK, TDI, TDO, TMS
6 | TPSQTP10SQ | TPSQTP10SQ | TP19, TP20, TP21, TP22, TP23, TP24
18 | TPSQTP16SQ | TPSQTP16SQ | TP1, TP2, TP3, TP4, TP5, TP6, TP7, TP8, TP9, TP10, TP11, TP12, TP13, TP14, TP15, TP16, TP17, TP18

### 1 UBB_MICRO_HIROSE UBB_MICRO_HIROSE U$4

1 | blue | LEDCHIP-LED0603 | LED3
1 | green | LEDCHIP-LED0603 | LED2
1 | red | LEDCHIP-LED0603 | LED1

file:///C:/Users/Fabi/Desktop/quadcopter_svn/versions/hardware V2.0 ...

1 von 1 | 13.09.2012 19:53

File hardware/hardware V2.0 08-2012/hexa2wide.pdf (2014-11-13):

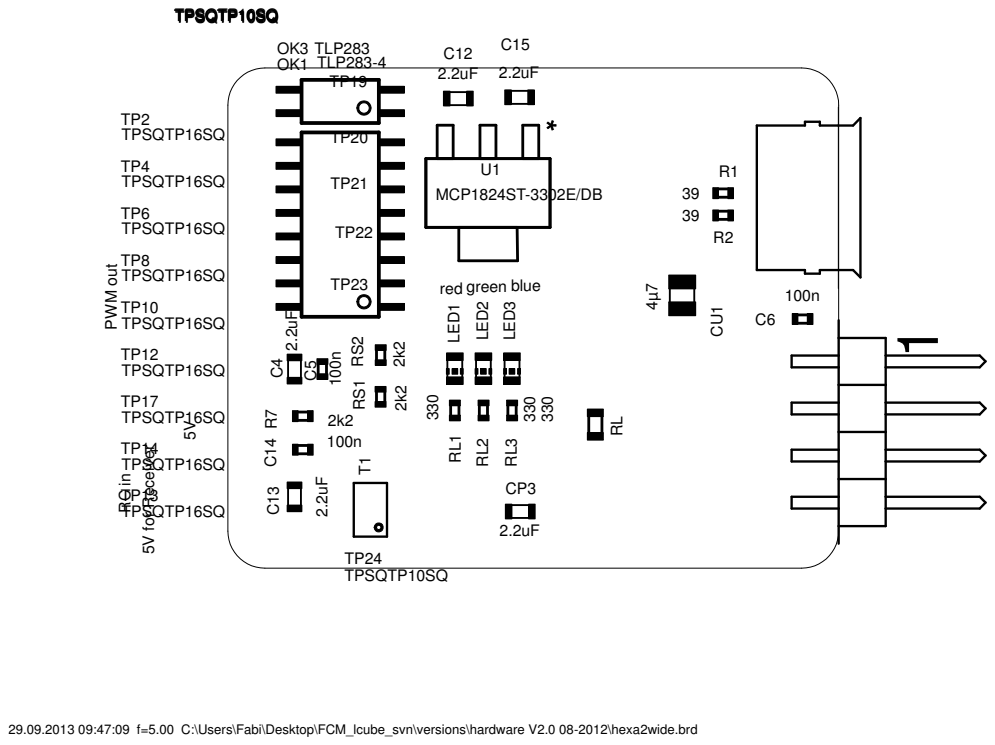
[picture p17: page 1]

29.09.2013 09:47:09 f=5.00 C:\Users\Fabi\Desktop\FCM_lcube_svn\versions\hardware V2.0 08-2012\hexa2wide.brd

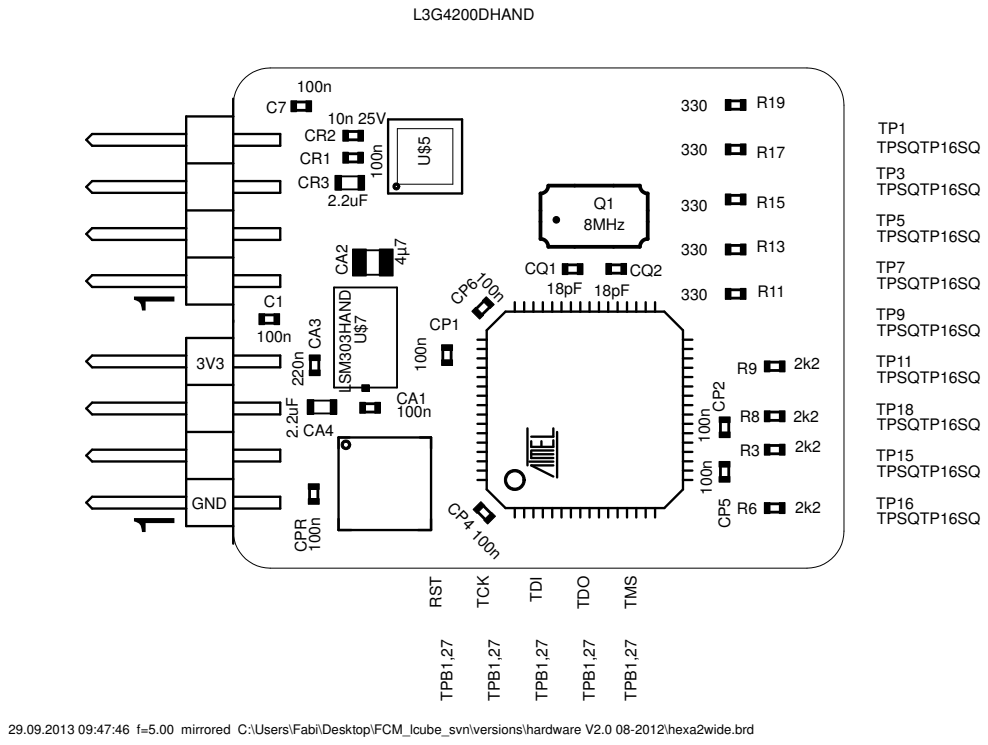
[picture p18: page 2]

29.09.2013 09:47:46 f=5.00 mirrored C:\Users\Fabi\Desktop\FCM_lcube_svn\versions\hardware V2.0 08-2012\hexa2wide.brd

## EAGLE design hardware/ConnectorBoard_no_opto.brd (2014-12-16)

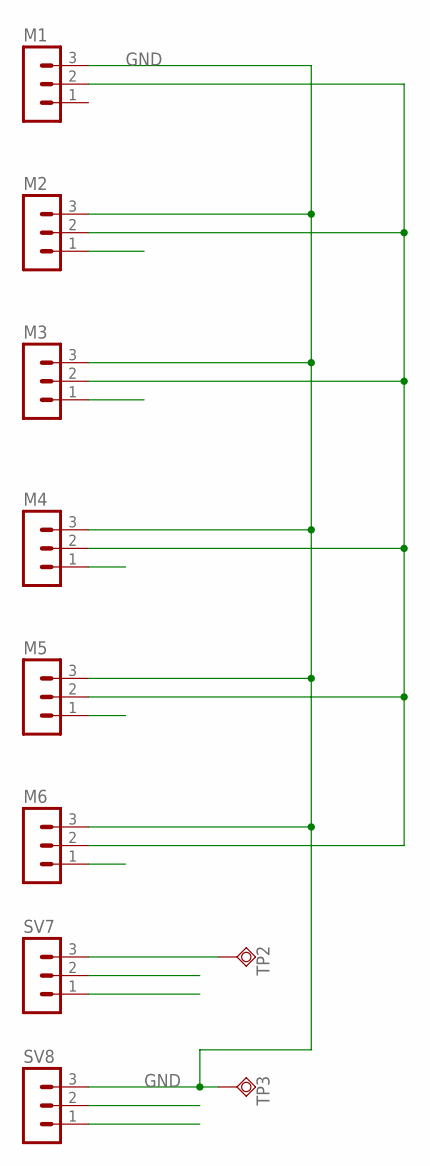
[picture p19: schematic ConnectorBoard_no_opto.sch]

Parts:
M1, M2, M3, M4, M5, M6: MA03-1
SV7, SV8: MA03-1
TP2, TP3: TPSQTP14SQ; TP14SQ

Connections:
GND: M1.3, M2.3, M3.3, M4.3, M5.3, M6.3, SV8.3, TP3.TP
unnamed: M1.2, M2.2, M3.2, M4.2, M5.2, M6.2
unnamed: SV7.3, TP2.TP

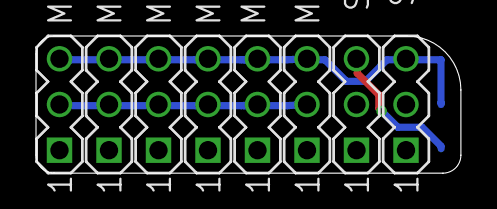
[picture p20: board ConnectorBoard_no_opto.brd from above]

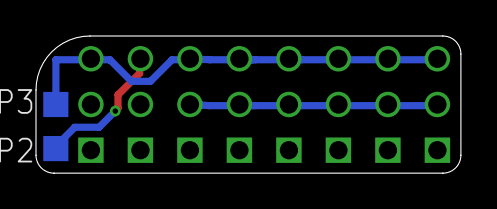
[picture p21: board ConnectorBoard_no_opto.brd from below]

Board: 2 copper layers, 23.6 x 7.6 mm, 10 parts (2 on the bottom side), 3 nets.

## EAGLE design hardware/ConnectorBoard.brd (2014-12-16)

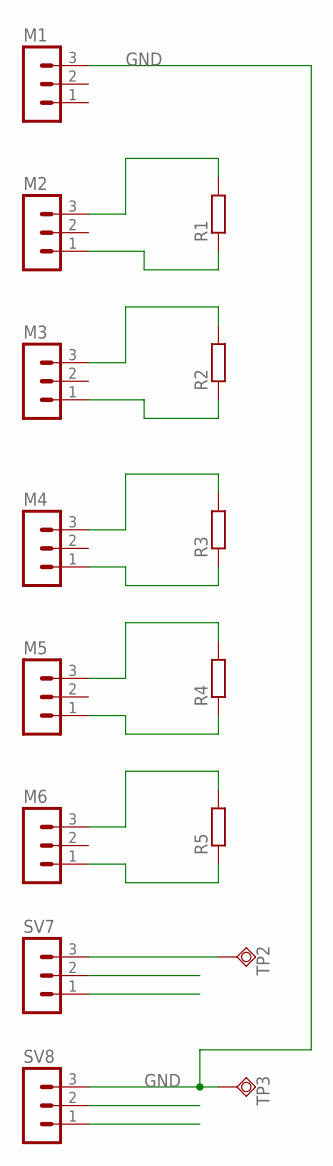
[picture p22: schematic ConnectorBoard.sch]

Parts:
M1, M2, M3, M4, M5, M6: MA03-1
R1, R2, R3, R4, R5: R-EU_R0402; R0402
SV7, SV8: MA03-1
TP2, TP3: TPSQTP14SQ; TP14SQ

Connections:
GND: M1.3, SV8.3, TP3.TP
unnamed: M3.3, R2.2
unnamed: M2.3, R1.2
unnamed: M2.1, R1.1
unnamed: M3.1, R2.1
unnamed: M4.3, R3.2
unnamed: M4.1, R3.1
unnamed: M5.3, R4.2
unnamed: M5.1, R4.1
unnamed: M6.3, R5.2
unnamed: M6.1, R5.1
unnamed: SV7.3, TP2.TP

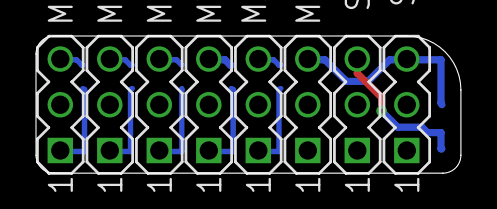
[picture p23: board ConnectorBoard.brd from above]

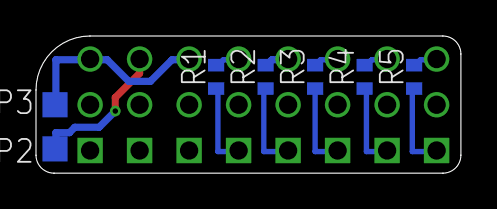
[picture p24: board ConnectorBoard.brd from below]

Board: 2 copper layers, 23.6 x 7.6 mm, 15 parts (7 on the bottom side), 12 nets.

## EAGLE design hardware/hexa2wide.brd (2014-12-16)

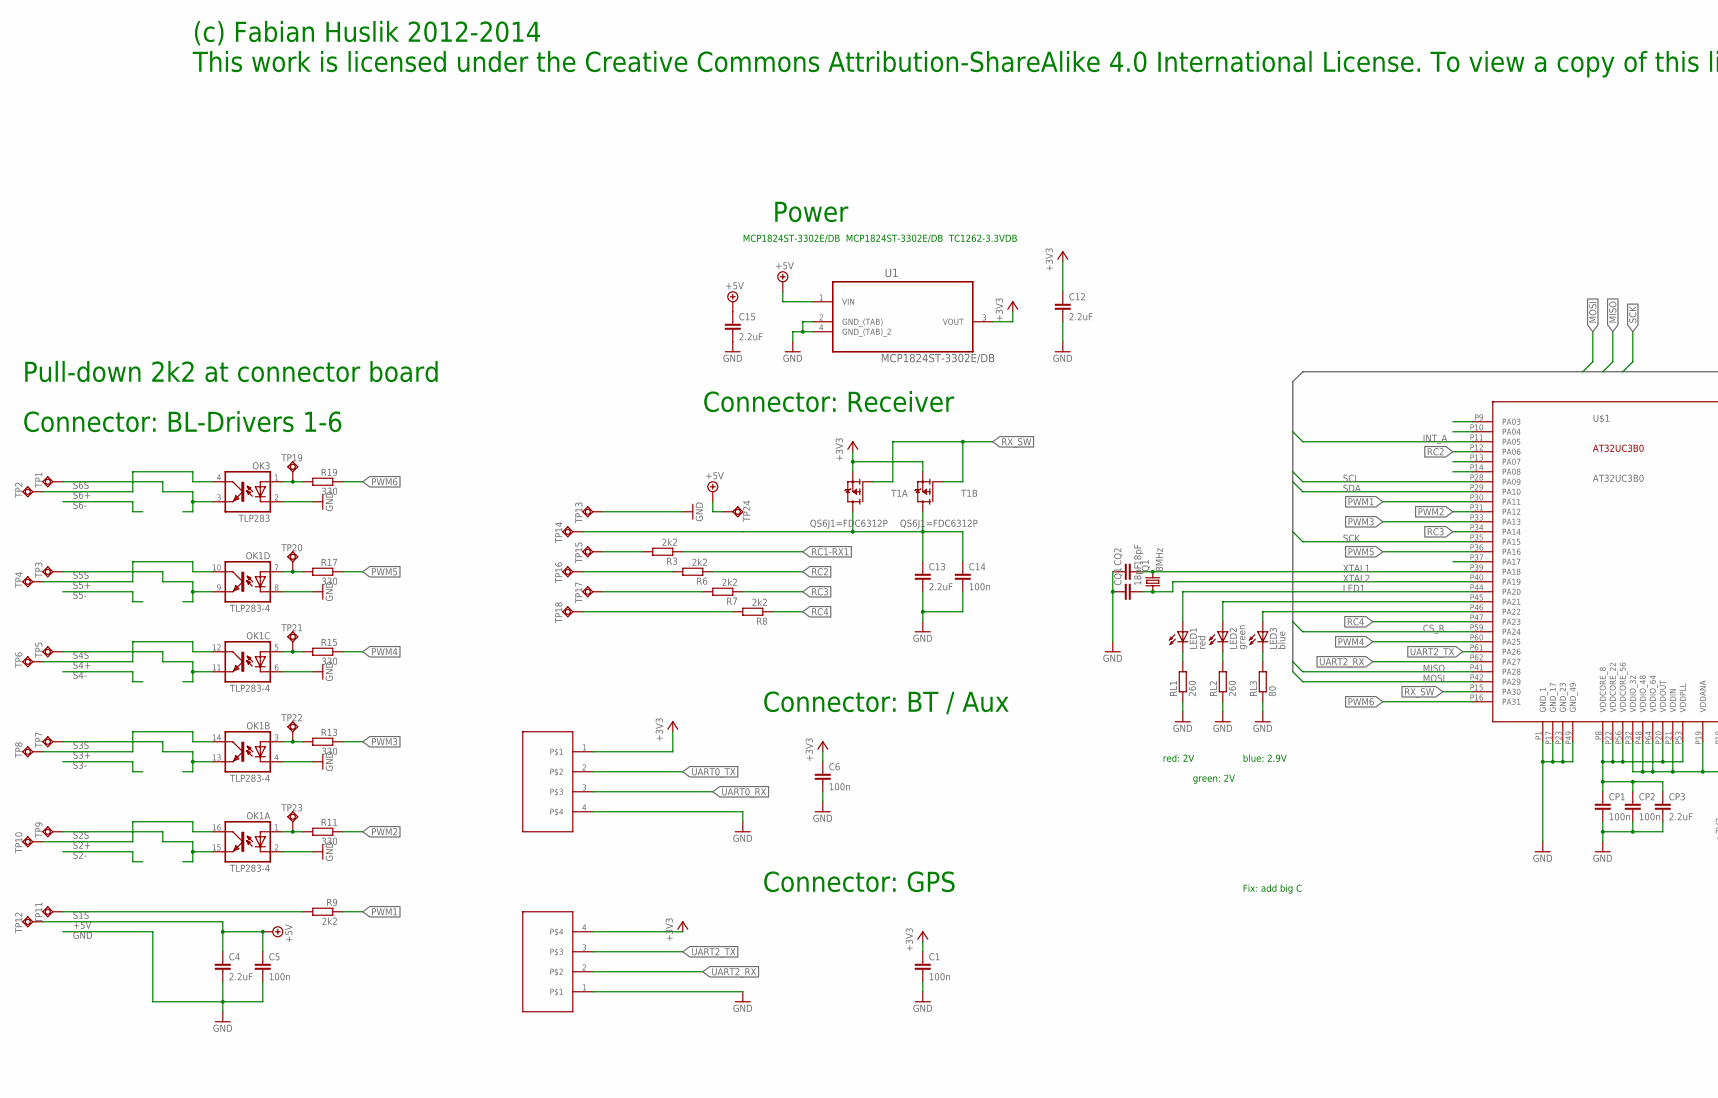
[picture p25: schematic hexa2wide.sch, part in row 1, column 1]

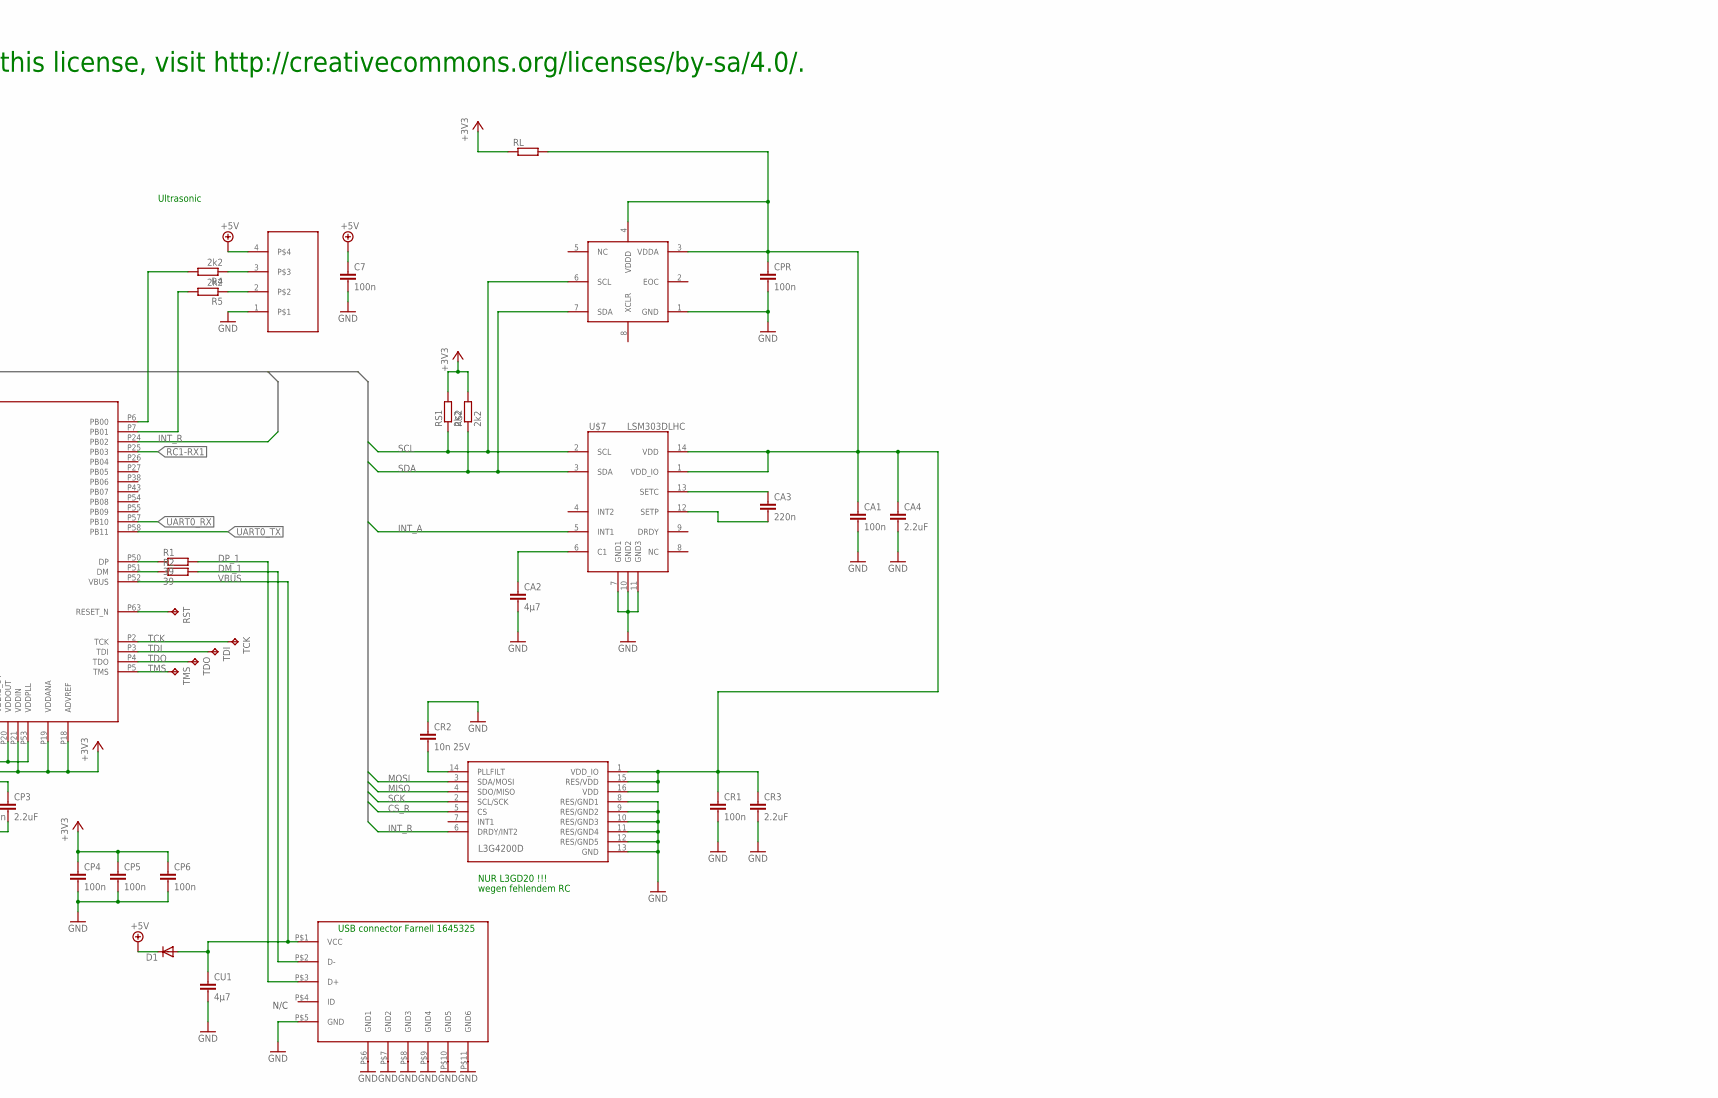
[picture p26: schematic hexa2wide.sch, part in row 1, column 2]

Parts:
C1, C5, C6, C7, C14: 100n; C0402; MPN MCCA000050
C4, C12, C13, C15: 2.2uF; C0603K; MPN GRM188R61C225KE15D
CA1: 100n; C0402; MPN MCCA000050
CA2: 4µ7; C0805; MPN GRM219R61C475KE15D
CA3: 220n; C0402; MPN C0402C224K9PACTU
CA4: 2.2uF; C0603K; MPN GRM188R61C225KE15D
CP1, CP2, CP4, CP5, CP6: 100n; C0402; MPN MCCA000050
CP3: 2.2uF; C0603K; MPN GRM188R61C225KE15D
CPR: 100n; C0402; MPN MCCA000050
CQ1, CQ2: 18pF; C0402; MPN C0402C180J5GACTU
CR1: 100n; C0402; MPN MCCA000050
CR2: 10n 25V; C0402; MPN MCCA000076
CR3: 2.2uF; C0603K; MPN GRM188R61C225KE15D
CU1: 4µ7; C0805; MPN GRM219R61C475KE15D
D1: DIODE-MICROMELF-R; MICROMELF-R
LED1: red; CHIP-LED0603; MPN ASMT-RR45-AQ902
LED2: green; CHIP-LED0603; MPN ASMT-RF45-AN002
LED3: blue; CHIP-LED0603; MPN SMLE12BC7TT86Q
OK1: TLP283-4; MINI-FLAT-16; MPN ACPL-247-500E
OK3: TLP283; MINI-FLAT-4; MPN ACPL-217-500E
Q1: 8MHz; CTS406; MPN ABMM2-8.000MHZ-E2-T
R1, R2: 39; R0402; MPN CRCW040239R0FKEAHP
R3, R4, R5, R6, R7, R8, R9: 2k2; R0402; MPN CRCW040210K5FKED
R11, R13, R15, R17, R19: 330; R0402; MPN MCMR04X331 JTL
RL: R-EU_R0603; R0603; MPN 74279266
RL1, RL2: 260; R0402; MPN CRCW0402604RFKED
RL3: 80; R0402; MPN ERJ2RKF8062X
RS1, RS2: 2k2; R0402; MPN CRCW040210K5FKED
RST: TPB1,27; B1,27
T1: QS6J1=FDC6312P; SUPERSOT-6; MPN FDC6312P
TCK: TPB1,27; B1,27
TDI: TPB1,27; B1,27
TDO: TPB1,27; B1,27
TMS: TPB1,27; B1,27
TP1, TP2, TP3, TP4, TP5, TP6, TP7, TP8, TP9, TP10, TP11, TP12, TP13, TP14, TP15, TP16, TP17, TP18: TPSQTP16SQ; TP16SQ
TP19, TP20, TP21, TP22, TP23, TP24: TPSQTP10SQ; TP10SQ
U1: MCP1824ST-3302E/DB; SOT230P700X180-4N; MPN MCP1824ST-3302E/DB
U$1: AT32UC3B0; JEDEC_MS-026; MPN AT32UC3B0256-A2UT
U$4: UBB_MICRO_HIROSE; USB_MICRO; MPN ZX62-B-5PA(11)
U$5: L3G4200DHAND; LGA16_HAND; MPN L3GD20
U$7: LSM303HAND; LGA14_HAND; MPN LSM303DLHC
U$9: BMP085
U$10, U$11, U$12: 4WIRE_CONN; 4WIRE_PIN

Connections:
1V6: CP1.1, CP2.1, CP3.1, U$1.P8 (VDDCORE_8), U$1.P20 (VDDOUT), U$1.P22 (VDDCORE_22), U$1.P53 (VDDPLL), U$1.P56 (VDDCORE_56)
+3V3: C1.1, C6.1, C12.1, CP4.1, CP5.1, CP6.1, RL.1, RS1.2, RS2.2, T1.P$2 (S), T1.P$5 (S), U1.3 (VOUT), U$1.P18 (ADVREF), U$1.P19 (VDDANA), U$1.P21 (VDDIN), U$1.P32 (VDDIO_32), U$1.P48 (VDDIO_48), U$1.P64 (VDDIO_64), U$10.4, U$11.1
+5V: C4.1, C5.1, C7.1, C15.1, D1.C, TP12.TP, TP24.TP, U1.1 (VIN), U$12.4
CS_R: U$1.P59 (PA24), U$5.5 (CS)
DM: R2.1, U$1.P51 (DM)
DM_1: R2.2, U$4.P$2 (D-)
DP: R1.1, U$1.P50 (DP)
DP_1: R1.2, U$4.P$3 (D+)
GND: C1.2, C4.2, C5.2, C6.2, C7.2, C12.2, C13.2, C14.2, C15.2, CA1.2, CA2.2, CA4.2, CP1.2, CP2.2, CP3.2, CP4.2, CP5.2, CP6.2, CPR.2, CQ1.1, CQ2.1, CR1.2, CR2.1, CR3.2, CU1.2, OK1.2 (C), OK1.4 (C), OK1.6 (C), OK1.8 (C), OK3.2 (C), RL1.1, RL2.1, RL3.1, TP13.TP, U1.2 (GND_(TAB)), U1.4 (GND_(TAB)_2), U$1.P1 (GND_1), U$1.P17 (GND_17), U$1.P23 (GND_23), U$1.P49 (GND_49), U$4.P$5 (GND), U$4.P$6 (GND1), U$4.P$7 (GND2), U$4.P$8 (GND3), U$4.P$9 (GND4), U$4.P$10 (GND5), U$4.P$11 (GND6), U$5.8 (RES/GND1), U$5.9 (RES/GND2), U$5.10 (RES/GND3), U$5.11 (RES/GND4), U$5.12 (RES/GND5), U$5.13 (GND), U$7.7 (GND1), U$7.10 (GND2), U$7.11 (GND3), U$9.1 (GND), U$10.1, U$11.4, U$12.1
INT_A: U$1.P11 (PA05), U$7.5 (INT1)
INT_R: U$1.P24 (PB02), U$5.6 (DRDY/INT2)
LED1: LED1.A, U$1.P44 (PA20)
MISO: U$1.P41 (PA28), U$5.4 (SDO/MISO)
MOSI: U$1.P42 (PA29), U$5.3 (SDA/MOSI)
unnamed: LED1.C, RL1.2
unnamed: RST.TP, U$1.P63 (RESET_N)
unnamed: CA3.1, U$7.13 (SETC)
unnamed: LED2.C, RL2.2
unnamed: LED3.C, RL3.2
unnamed: LED2.A, U$1.P45 (PA21)
unnamed: LED3.A, U$1.P46 (PA22)
unnamed: CR2.2, U$5.14 (PLLFILT)
unnamed: CA2.1, U$7.6 (C1)
unnamed: CA3.2, U$7.12 (SETP)
unnamed: R3.2, TP15.TP
unnamed: C13.1, C14.1, T1.P$4 (D), T1.P$6 (D), TP14.TP
unnamed: R6.2, TP16.TP
unnamed: R7.2, TP17.TP
unnamed: R8.2, TP18.TP
unnamed: OK1.1 (A), R11.2, TP23.TP
unnamed: OK1.3 (A), R13.2, TP22.TP
unnamed: OK1.5 (A), R15.2, TP21.TP
unnamed: R4.1, U$12.3
unnamed: R5.1, U$12.2
unnamed: OK1.7 (A), R17.2, TP20.TP
unnamed: OK3.1 (A), R19.2, TP19.TP
PWM1: R9.1, U$1.P30 (PA11)
PWM2: R11.1, U$1.P31 (PA12)
PWM3: R13.1, U$1.P33 (PA13)
PWM4: R15.1, U$1.P60 (PA25)
PWM5: R17.1, U$1.P36 (PA16)
PWM6: R19.1, U$1.P16 (PA31)
RC1-RX1: R3.1, U$1.P25 (PB03)
RC2: R6.1, U$1.P12 (PA06)
RC3: R7.1, U$1.P34 (PA14)
RC4: R8.1, U$1.P47 (PA23)
RX_SW: T1.P$1 (G), T1.P$3 (G), U$1.P15 (PA30)
S1S: R9.2, TP11.TP
S2+: OK1.16 (COL), TP10.TP
S2S: OK1.15 (EMIT), TP9.TP
S3+: OK1.14 (COL), TP8.TP
S3S: OK1.13 (EMIT), TP7.TP
S4+: OK1.12 (COL), TP6.TP
S4S: OK1.11 (EMIT), TP5.TP
S5+: OK1.10 (COL), TP4.TP
S5S: OK1.9 (EMIT), TP3.TP
S6+: OK3.4 (COL), TP2.TP
S6S: OK3.3 (EMIT), TP1.TP
SCK: U$1.P35 (PA15), U$5.2 (SCL/SCK)
SCL: RS1.1, U$1.P28 (PA09), U$7.2 (SCL), U$9.6 (SCL)
SDA: RS2.1, U$1.P29 (PA10), U$7.3 (SDA), U$9.7 (SDA)
TCA0: R4.2, U$1.P6 (PB00)
TCB0: R5.2, U$1.P7 (PB01)
TCK: TCK.TP, U$1.P2 (TCK)
TDI: TDI.TP, U$1.P3 (TDI)
TDO: TDO.TP, U$1.P4 (TDO)
TMS: TMS.TP, U$1.P5 (TMS)
UART0_RX: U$1.P57 (PB10), U$11.3
UART0_TX: U$1.P58 (PB11), U$11.2
UART2_RX: U$1.P62 (PA27), U$10.2
UART2_TX: U$1.P61 (PA26), U$10.3
VBUS: CU1.1, D1.A, U$1.P52 (VBUS), U$4.P$1 (VCC)
VCCSENS: CA1.1, CA4.1, CPR.1, CR1.1, CR3.1, RL.2, U$5.1 (VDD_IO), U$5.15 (RES/VDD), U$5.16 (VDD), U$7.1 (VDD_IO), U$7.14 (VDD), U$9.3 (VDDA), U$9.4 (VDDD)
XTAL1: CQ2.2, Q1.3 (2), U$1.P39 (PA18)
XTAL2: CQ1.2, Q1.1, U$1.P40 (PA19)

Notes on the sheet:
USB connector Farnell 1645325
Connector: Receiver
Connector: BL-Drivers 1-6
Power
Connector: GPS
N/C
NUR L3GD20 !!!
wegen fehlendem RC
Connector: BT / Aux
Ultrasonic
MCP1824ST-3302E/DB MCP1824ST-3302E/DB TC1262-3.3VDB
red: 2V
green: 2V
blue: 2.9V
Pull-down 2k2 at connector board
Fix: add big C
This work is licensed under the Creative Commons Attribution-ShareAlike 4.0 International License. To view a copy of this license, visit http://creativecommons.org/licenses/by-sa/4.0/.
(c) Fabian Huslik 2012-2014

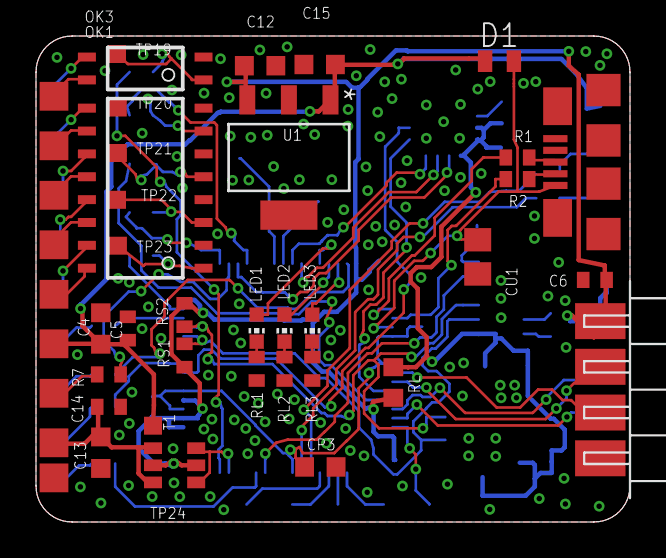
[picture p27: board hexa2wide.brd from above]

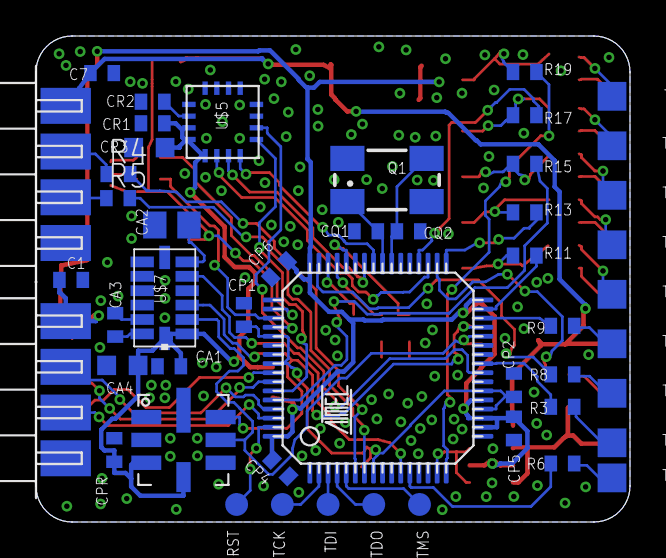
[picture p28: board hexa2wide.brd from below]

Board: 2 copper layers, 33.0 x 27.0 mm, 92 parts (49 on the bottom side), 75 nets.

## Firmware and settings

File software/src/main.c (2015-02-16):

/*
   ___ _ _      _   _      ___         _           _   __  __         _      _
  | __| (_)__ _| |_| |_   / __|___ _ _| |_ _ _ ___| | |  \/  |___  __| |_  _| |___
  | _|| | / _` | ' \  _| | (__/ _ \ ' \  _| '_/ _ \ | | |\/| / _ \/ _` | || | / -_)
  |_| |_|_\__, |_||_\__|  \___\___/_||_\__|_| \___/_| |_|  |_\___/\__,_|\_,_|_\___|
    ____  |___/ __  _ _ _    ___     _    _             _  _         _ _ _
   / /\ \  |_  )  \/ | | |  | __|_ _| |__(_)__ _ _ _   | || |_  _ __| (_) |__
  | / _| |  / / () | |_  _| | _/ _` | '_ \ / _` | ' \  | __ | || (_-< | | / /
  | \__| | /___\__/|_| |_|  |_|\__,_|_.__/_\__,_|_||_| |_||_|\_,_/__/_|_|_\_\
   \_\/_/
 
 
  (c) 2012-2015 by Fabian Huslik
 
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
 
 in linker configuration the flag ,--relax has been removed to prevent the "input not relaxable" error.

!!!!!!!!!!!!!!!!!!!!!!!!!!!!!!!!!!!!!!!!!!!!!!!!!!!!!!!!!!! 
Important: The -ffunctions-sections in gcc and the -Wl,--gc-sections in linker must be omitted !!!
!!!!!!!!!!!!!!!!!!!!!!!!!!!!!!!!!!!!!!!!!!!!!!!!!!!!!!!!!!!
 */

#include <asf.h>
#include "modules/types.h"
#include "modules/vector.h"
#include "FabOS_config.h"
#include "FabOS/FabOS.h"
#include "gyro.h"
#include "modules/servo_out.h"
#include "servo_in.h"
#include "modules/hottv4.h"
#include "menu/menu.h"
#include "modules/CRC_CCITT.h"
#include "modules/emergency.h"
#include "config.h"
#include "modules/testsuite.h"
#include "TaskControl.h" // for LED fumbling
#include "TaskLED.h" // for LED fumbling

OS_DeclareTask(TaskControl,800);
OS_DeclareTask(TaskTWI,500);
OS_DeclareTask(TaskComm2,800);
OS_DeclareTask(TaskComm0,800);
OS_DeclareTask(TaskLED,500);
OS_DeclareTask(TaskMenu,800);
OS_DeclareTask(TaskNavi,500);

extern void init_pins(void);
extern void init_xtal_pll(void);

#define NO_OS 0

#if NO_OS == 1
	extern void TaskTWI_NO_OS(void);
#endif

int main( void )
{
	OS_DISABLEALLINTERRUPTS; // BL could have been running
	//disable USB ISR !!
	AVR32_USBB.usbcon = 0x03004000; // switch off all interrupts (reset value)
	AVR32_USBB.udcon  = 0x00000100; // detach
	AVR32_USBB.udintclr = 0xffffffff; // disable all ISRs
	
	
	init_xtal_pll();
	init_pins();
	
	// fixme enable BOD
	
	if(AVR32_PM.RCAUSE.por || AVR32_PM.RCAUSE.bod)
	{
		LED_RED_ON;
	}
	else if (AVR32_PM.RCAUSE.wdt)
	{
		LED_RED_ON;
		LED_GREEN_ON;
		LED_BLUE_ON;
		// fixme create fast path to "flight" if this happens!!!
		// meanwhile we crash here
		//emstop(12);
	}
	wdt_opt_t wdopt;
	wdopt.us_timeout_period = 10000000; // 10s // this is the only one parameter.
	wdt_enable(&wdopt); // enable WD
	
	INTC_init_interrupts();
	
	init_crcccitt_tab(); // prepare table for fast CRC calculation

#if NO_OS == 1
	delay_init(BOARD_SYS_HZ);
	OS_ENABLEALLINTERRUPTS;
	while(1)
	{
		TaskTWI_NO_OS(); // debug
		delay_ms(10);
	}

#endif


	#if TEST_RUN == 1
	#warning running unit tests
	test_run();
	
	//while(1); // continue after tests, as failed tests will hang.

	#endif


		
	OS_InitTiming(); 

	// start OS as early as possible and let init the tasks their HW themselves.
	
	#if OS_DO_TESTSUITE == 1
	OS_TestSuite(); // call automated tests of OS. may be removed in production code.
	#endif
	
	OS_CreateTask(TaskControl, OSTSK_CONTROL);
	OS_CreateTask(TaskTWI, OSTSK_TWI);
	OS_CreateTask(TaskComm0, OSTSK_COMM0);
	OS_CreateTask(TaskComm2, OSTSK_COMM2);
	OS_CreateTask(TaskLED, OSTSK_LED);
	OS_CreateTask(TaskMenu, OSTSK_MENU);
	OS_CreateTask(TaskNavi, OSTSK_NAVI);

	OS_CreateAlarm(OSALM_CTRLWAIT,OSTSK_CONTROL);
	OS_CreateAlarm(OSALM_TWIWAIT,OSTSK_TWI);
	OS_CreateAlarm(OSALM_COMM0WAIT,OSTSK_COMM0);
	OS_CreateAlarm(OSALM_COMM2WAIT,OSTSK_COMM2);
	OS_CreateAlarm(OSALM_LEDWAIT,OSTSK_LED);
	OS_CreateAlarm(OSALM_MENUWAIT,OSTSK_MENU);
	OS_CreateAlarm(OSALM_NAVIWAIT,OSTSK_NAVI);
	OS_CreateAlarm(OSALM_TWITIMEOUT,OSTSK_TWI);

	OS_StartExecution() ;
	while(1)
	{
		 // the idle task	
		 
		// you could do phantastic things here...

	}
}	


	


/*
static volatile int32_t rec[100];
static volatile int32_t rcnt;

extern void RecordValue( int32_t v );
//RecordValue(*z);

void RecordValue( int32_t v )
{
	rec[rcnt] = v;
	rcnt++;

	if(rcnt >= 100)
	{
		rcnt = 0;
	}
}
*/


#if OS_USEEXTCHECKS == 1
void OS_ErrorHook(uint8_t ErrNo)
{
	static uint8_t dummy =0;
	
	switch(ErrNo)
	{
		case 2:
			// OS_WaitEvent: waiting in idle is not allowed
			break;	
		case 4:
			// OS_WaitAlarm: waiting in idle is not allowed
			break;
		case 5:
			// OS_MutexGet: invalid Mutex number
			break;
		case 6:
			// OS_MutexRelease: invalid Mutex number
			break;
		case 7:
			// OS_Alarm misconfiguration
			break;
		case 8:
			// OS_WaitAlarm: Alarm was not active
			break;
		case 9:
			// OS_WaitAlarm: Alarm is not assigned to the task (critical!)
			break;
		case 10:
			// Scheduler: Task seems to be waiting inside Mutex
			break;
		case 99:
			// spare
			break;
		default:
			break;	
	}
	
	dummy = ErrNo; // dummy code

	#if OS_DO_TESTSUITE == 1
	asm("breakpoint"); // for automated tests of OS. may be removed in production code.
	#endif
	asm("breakpoint"); // for manual test too...
}
#endif

void OS_ShutdownHook(uint8_t reason)
{
	static uint8_t dummy =0;
	dummy = reason;
	OS_DISABLEALLINTERRUPTS;
	while(1)
	{
		asm("breakpoint");
		wdt_reset_mcu(); // only works, if wd is enabled
	}
}

void OS_CustomISRCode(void)
{
	// reset timer here instead in isr?	
}

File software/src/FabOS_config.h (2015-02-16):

/*
	FabOS for ATMEL AVR32 user configuration file
	
	(c) 2008-2015 Fabian Huslik
    
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
	Please change this file to your needs.
*/

// *********  USER Configurable Block BEGIN
#define OS_DO_TESTSUITE 0	// compile and execute the automated software tests. Set to 0 for production use of OS.

#if OS_DO_TESTSUITE == 0

#define OS_NUMTASKS  7 // Number of (OS_Create)Tasks ; never >64 (idle task is not counted here!)
#define OS_NUMMUTEX  2 // Number of Mutexes
#define OS_NUMALARMS 8 // Number of Alarms // todo maybe count

#define OS_USECLOCK 1 		// Use "OS_GetTicks()" which returns a 32bit timer tick
#define OS_USECOMBINED 1 	// Use "OS_WaitEventTimeout()" which is easier to use, than combining alarms and events to get the functionality.
#define OS_USEEXTCHECKS 1	// check wrong usage of OS API -> does not work, but no damage to OS stability.
#define OS_USEMEMCHECKS 1 	// Enable "OS_get_unused_Stack()" and "OS_GetQueueSpace()"
#define OS_UNUSEDMASK 0xEEEEEE00  // unused Stack RAM will be filled with this byte, if OS_USEMEMCHECKS == 1.
#define OS_TRACE_ON  0 		// enable trace to OS_Tracebuffer[]
#define OS_TRACESIZE 1000	// size of OS_Tracebuffer[] (depending on memory left ;-)

#endif

// Task definitions = priorities, 0 = highest
#define OSTSK_TWI 0
#define OSTSK_COMM0 1	// high prio for HoTT (Exact timing)
#define OSTSK_CONTROL 2
#define OSTSK_COMM2 3	// GPS
#define OSTSK_LED 4
#define OSTSK_NAVI 5
#define OSTSK_MENU 6

// Event Names (Event is a bit in a bitfield !!!!)
#define OSEVT_CTLWAKEUP  (1<<0)
#define OSEVT_GPSREADY   (1<<1)
#define OSEVT_MENUWAKEUP (1<<2)
#define OSEVT_MAVRX		 (1<<3)
#define OSEVT_TWIRDY     (1<<4)

// Mutex Names
#define OSMTX_COMM 0
#define OSMTX_TWI 1

// Alarm Names
#define OSALM_CTRLWAIT	0
#define OSALM_TWIWAIT	1
#define OSALM_COMM0WAIT	2
#define OSALM_COMM2WAIT	3
#define OSALM_LEDWAIT	4
#define OSALM_MENUWAIT	5
#define OSALM_NAVIWAIT	6
#define OSALM_TWITIMEOUT 7



// *********  USER Configurable Block END 


#if OS_DO_TESTSUITE == 1

#define OS_NUMTASKS  5 // Number of (OS_Create)Tasks ; never >64 (idle task is not counted here!)
#define OS_NUMMUTEX  3 // Number of Mutexes
#define OS_NUMALARMS 6 // Number of Alarms

#define OS_USECLOCK 1 		// Use "OS_GetTicks()" which returns a 32bit timer tick
#define OS_USECOMBINED 1 	// Use "OS_WaitEventTimeout()" which is easier to use, than combining alarms and events to get the functionality.
#define OS_USEEXTCHECKS 1	// check wrong usage of OS API -> does not work, but no damage to OS stability.
#define OS_USEMEMCHECKS 1 	// Enable "OS_get_unused_Stack()" and "OS_GetQueueSpace()"
#define OS_UNUSEDMASK 0xDEAD0000  // unused Stack RAM will be filled with this byte, if OS_USEMEMCHECKS == 1.
#define OS_TRACE_ON  1 		// enable trace to OS_Tracebuffer[]
#define OS_TRACESIZE 1000	// size of OS_Tracebuffer[] (depending on memory left ;-)

#endif

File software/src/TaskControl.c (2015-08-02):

/*
 * TaskControl.c
 * This is where the magic happens (most of)
 *
 * Created: 06.09.2012 09:40:25
 *
 * (c) 2012-2015 by Fabian Huslik
 *
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
 fixme FIXME todo TODO (yepp) This whole file needs complete rework!
 
 git rev-parse --short=8 HEAD
 
 */   

#include <asf.h>
#include <fastmath.h>
#include "modules/types.h"
#include "modules/vector.h"
#include "FabOS_config.h"
#include "FabOS/FabOS.h"
#include "modules/spi.h"
#include "gyro.h"
#include "l3gd20.h"
#include "modules/servo_out.h"
#include "servo_in.h"
#include "UsartRC.h"
#include "menu/menu.h"
#include "menu/menu_variant.h"
#include "FabOS_config.h"
#include "FabOS/FabOS.h"
#include "TaskControl.h"
#include "TaskLED.h"
#include "TaskTWI.h"
#include "modules/fcmcp.h"
#include "modules/quaternions/quaternions.h"
#include "modules/quaternions/MadgwickAHRS.h"
#include "modules/quaternions/MahonyAHRS.h"
#include "modules/quaternions/AHRS2.h" // in test !
#include "modules/emergency.h"
#include "modules/magnetics_calibration.h"
#include "modules/vector.h"
#include "modules/governing.h"
#include "modules/ParFlash.h"
#include "config.h"
#include "modules/GPS.h"
#include "modules/NAV.h"
#include "TaskNavi.h"
#include "modules/usart.h"
#include "modules/SIM.h"
#include "version.h"

void TaskControl(void);
void acc_calibrate(vector3_t* g);
void LoadParameters(void); 

fcm_data_t TXData; // data to be sent via FCMCP // todo maybe make a common buffer
fcm_quaternion_t TXQuaternions;
fcm_GPSdata_t TXGPSdata;

float debug_der_x; 
float debug_der_y;

IMUdata_t IMUdata; // info stuff

#define HEIGHTINITFILTER 10

uint32_t debug_RunTimeMax=0;
bool swAUX; // fixme global

/*

Servo input scaling:

throttle = 1000 = idle - 9000 full
roll: -4000 = right +4000 = left
elev : +4000 nose down -4000 nose up
yaw: -4000 = right +4000 = left

*/

void LoadParameters(void) 
{
	int16_t pardata_raw[MENUE_PARCOUNT];
	static int16_t* pdata;
	
	pdata = (int16_t*)(&myPar);
	
	int ret = ParFlash_load((uint8_t*)&pardata_raw, MENUE_PARCOUNT*2, PARAMETERVERSION); // we use them here, we load them here.
	
	if (ret == 0)
	{
		// load array of values only...
		for (int i = 0; i < MENUE_PARCOUNT;i++)
		{
			*pdata = pardata_raw[i];
			pdata += sizeof(Parameter_t)/2; // 2-byte-pointer
		}
	}
}

void TaskControl(void)
{
	static int32_t cmd_thr, cmd_roll, cmd_elev, cmd_yaw; // debug static
	
	bool swPosHold,swHGov,swRTH; // RC switch states
	int32_t pct; // fix name
	
	// measurement vectors
	vector3_t v_gyro_raw;
	vector3_t v_gyro_radps;
	vector3_t v_acc_frame_mpss; // includes gravity
	vector3_t v_acc_global_mpss; // without gravity, rotated into global frame
	vector3_t v_mag; 
	
	int32_t temperature_degC;

	quaternion_t q_ActualOrientation; // the actual rotation in global frame
	static quaternion_t q_RC_Set = {1,0,0,0}; // the official setpoint for the orientation.
	quaternion_t q_nav_global;
	quaternion_t q_set_global; // combined nav and rc

	float fActHeading_rad;
	
	vector3_t v_TrgDistance_m; // the distance to the target

	static float fSetHeading_rad = 0.0; // fixme also possible without this?? (one rc-input-quaternion, the rotation integration takes place by the frame itself)
	
	
	quaternion_t q_Diff;
	vector3_t v_diff_rad; // euler difference actual->set in rad

	int32_t ox, oy, oz, oa=0; // the output values for the output mixer
	static pid_t s_t_pid_x, s_t_pid_y, s_t_pid_z; // Gyro PID static values

	static vector3_t gyro_cal,acc_cal,mag_cal; // calibration values

	float dummy1,dummy2; // dummy results, needed as pointers

	//vector3_t v_RCCommand_rad;

	vector3_t res_cmd; // fixme change into rotation speed rad/s or so.

	int RCtimeout;
	
	static uint32_t RunTime; // run time measurement
	static uint32_t RunTimeStart=0; // run time measurement - remember the start time
	
	
	// globals from the best algo - ever
	vector3_t v_pos_act_m = {0.0,0.0,0.0}; // actual position offset from origin (global)
	
	vector3_t v_pos_target_m;
	static vector3_t v_pos_last_m;
	
	float ax,ay; // fixme name
	vector3_t v_accel_command_mpss;
	vector2_t bank;
	
	
	LoadParameters();
	
	if(myPar.DirectMode.sValue != 0)
	{
		// wait for RX to get a signal before sending out the PWM (Servo signal)
		OS_WaitTicks(OSALM_CTRLWAIT,1000); 
	}
	
	acc_cal.x = (float)myPar.cal_acc_x.sValue/1000.0;
	acc_cal.y = (float)myPar.cal_acc_y.sValue/1000.0;
	acc_cal.z = (float)myPar.cal_acc_z.sValue/1000.0;
	gyro_cal.x = myPar.cal_gyro_x.sValue;
	gyro_cal.y = myPar.cal_gyro_y.sValue;
	gyro_cal.z = myPar.cal_gyro_z.sValue;
	mag_cal.x =  myPar.cal_mag_x.sValue;
	mag_cal.y =  myPar.cal_mag_y.sValue;
	mag_cal.z =  myPar.cal_mag_z.sValue;


	SPI_init();
	gyro_init();

	servo_in_init(OSALM_CTRLWAIT);
	servo_out_init(); // init outputs AFTER inputs, otherwise the calibration will not work.

	
	LED_SetFlightstate(FS_init);
	
	while(1)
	{
		wdt_clear(); // kick the dog
		
		RunTime = OS_GetTicks()-RunTimeStart; // "end" of runtime-measurement
		debug_RunTimeMax = max(debug_RunTimeMax,RunTime);
		OS_WaitEvent(OSEVT_CTLWAKEUP); //wait for isr, which synchronizes this task with the pwm output.
		RunTimeStart = OS_GetTicks(); // start of runtime-measurement
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

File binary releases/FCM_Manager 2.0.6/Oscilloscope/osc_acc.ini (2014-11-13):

[Oscilloscope]
OscVrulFontName=Arial
OscVrulFontSize=8
OscVrulFontStyleBold=0
OscVrulFontStyleItalic=0
OscBackColor=00222222
OscGridColor=00404040
OscHorScaleColor=00FFFFFF
OscBeam0Color=000000FF
OscBeam1Color=0000FF00
OscBeam2Color=00FF0000
OscVrulGenFontColor=00FFFFFF
OscZeroLineColor=00FFFFFF
OscOscCaption=Accelerometer Data
ShowSecondBeam=1
ShowThirdBeam=1
ShowTestButton=0
BuffersRecordType=1
CreateSecondBeam=1
CreateThirdBeam=1
SpreadViewTiming=1
EventsProcDivider=0
GridRefreshDivider=50
GridCellPixelsSize=20
TriggerEnable=0
TriggerSource=0
FirstTriggerLevel=0.0000000000
SecondTriggerLevel=0.0000000000
ThirdTriggerLevel=0.0000000000
ExtrnTriggerLevel=0.0000000000
TimeSamplesPerCell=100.0000000000
Beam0VertScale=10000.0
Beam1VertScale=10000.0
Beam2VertScale=10000.0
Beam0VertOffset=0.0000000000
Beam1VertOffset=0.0000000000
Beam2VertOffset=0.0000000000
ScopeFormTop=96
ScopeFormLeft=21
ScopeFormHeight=600
ScopeFormWidth=800
ScopeStayOnTop=0
ShowTriggerControls=0
ShowOscJaggies=0
ShowOscHexVal=0
ShowHexCheckBox=0
ScopeShowAutoSweep=1
ScopeAutoSweep=0
ScopeAutoSweepDivider=4
ScopeShowHints=1
Producer_Vendor_Name=+972 507669424 Michael Bernstein, E_Mail: brnstin@cheerful.com
BfrSmplSize=32000
ScopeInputDumpSize=32000
ScopePolylineOptimize=0
[Miscellaneous]
ReadDelayPerSample=0

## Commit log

2014-11-12 added the whole project.
    [ConnectorBoard.brd, ConnectorBoard.sch, ConnectorBoard_no_opto.brd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]
2014-11-12 added hw versions and de-automatized versioning
    [ConnectorBoard.brd, ConnectorBoard.sch, ConnectorBoard_no_opto.brd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]
2014-11-26 fix sim aerodynamic resistance error
    keep a build error on purpose, fix next time.
    [TaskControl.c]
2014-11-28 fix switch over between modes
    [TaskControl.c]
2014-11-29 fixed som rotational problems and H-governor switch
    [TaskControl.c]
2014-11-29 NAV working now in sim.
    changed PID scaling; new nav parameters,
    NAV working now in sim.
2014-11-30 implement sensor simulation
2014-11-30 avoid going down far away from home at RTH+ Display the simulated orientation
    [TaskControl.c]
2014-12-04 do aerodynamics in vehicle frame
2014-12-16 update hw to eagle 7.2
    [ConnectorBoard.brd, ConnectorBoard.sch, ConnectorBoard_no_opto.brd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]
2014-12-26 improve filtering - to be tested
2014-12-30 basic simulation running again, gyro simulation delivers implausible values right before liftoff.
2015-01-01 remove velocity
2015-01-11 switch on the sensor fusion ....
2015-01-19 quaternion vector rotation not working
    [TaskControl.c, main.c]
2015-02-11 Revert "some corrections"
    This reverts commit a371bd67a5920ac6f6e5a271a302a40648084823.
    [l3gd20.c]
2015-04-12 make filtered stuff static
2015-04-21 updated and fixed nav governor with filter, which kills about 400ms of GPS delay.
    [TaskControl.c]
2015-05-15 move filter code to governing.h
2015-05-20 fixed h startup + parameters
    fixed h reset to 0 at start
    [TaskControl.c]

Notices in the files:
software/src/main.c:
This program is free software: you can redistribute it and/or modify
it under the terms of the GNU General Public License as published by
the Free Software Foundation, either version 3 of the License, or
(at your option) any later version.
